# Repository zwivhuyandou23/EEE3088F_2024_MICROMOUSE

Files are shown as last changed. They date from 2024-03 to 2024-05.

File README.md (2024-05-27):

# Welcome to the EEE3088F_2024_MICROMOUSE hardware project

## Name
 2024 Micromouse Project

## Description
The Micromouse Project is a maze-solving robot project designed for the EEE3088F 2024 course. Students will focus on designing and manufacturing sensor and power modules for the micro-mouse, meeting specific project requirements while adhering to a strict budget.

## Features
- Sensor module for detecting obstacles
- Power module for powering the entire system
- Integration with provided motherboard and processor boards

## Project Scenarios
Maze completion.

## Usage
The Micromouse project is intended for educational purposes in the EEE3088F 2024 course. Zwivhuya Ndou and Innocent Makhubela worked on designing, manufacturing, and demonstrating the sensor and power modules for the micro-mouse robot.

## Installation
To access some of the contents on the repo you will need kicad to open the project PCB, Schematics designs and an IDE that supports C programming

## Authors and acknowledgment
Zwivhuya Ndou, Innocent Makhubela

## Contributing

Contributions to the ENVIRO-SENSING-HAT project are welcome! If you have any ideas, bug fixes, or improvements, please follow the guidelines outlined in the [CONTRIBUTING.md](CONTRIBUTING.md) file.

## License

The ENVIRO-SENSING-HAT project is licensed under the MIT License. See the [LICENSE](LICENSE.md) file for more information.

## Project status
Ongoing - part of the EEE3088F 2024 course project, to be carried to the second semester course.

## Contact
If you have any questions or inquiries about the Micromouse project, feel free to contact us at Zwivhuya Ndou(ndxzwi002@myuct.ac.za), Innocent Makhubela ().

Thank you for your interest in the Micromouse project!

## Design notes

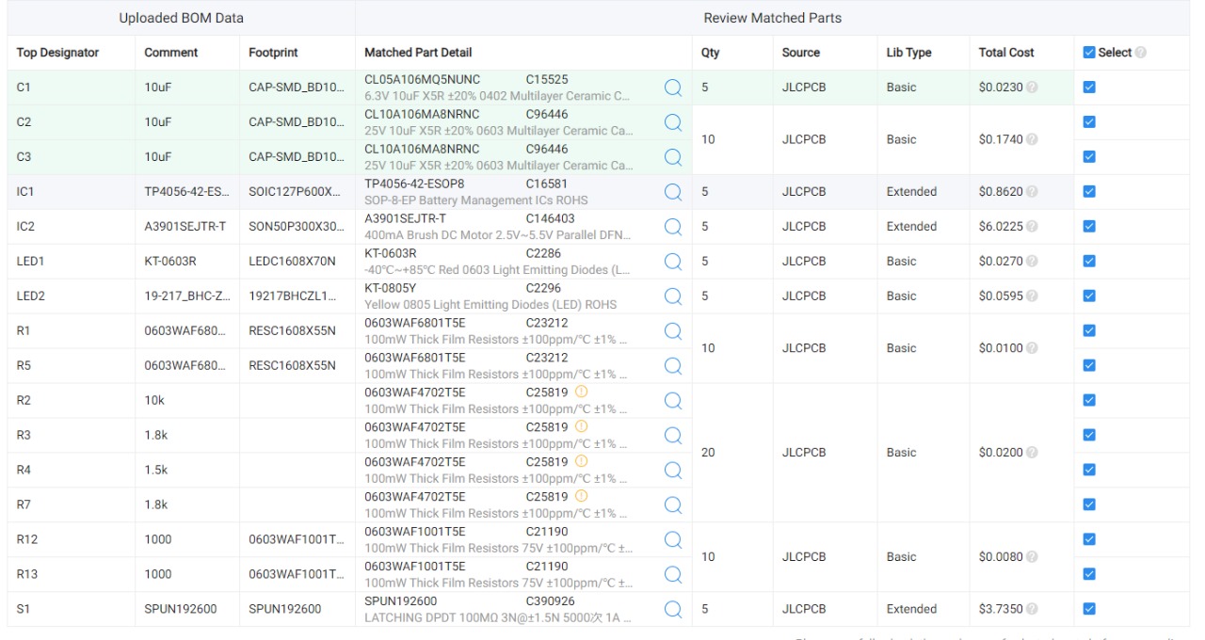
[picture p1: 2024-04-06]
Design/Power/Kicad/production_files/EEE3088F_Project_JLCPCBBOM_MKHINN011.jpg

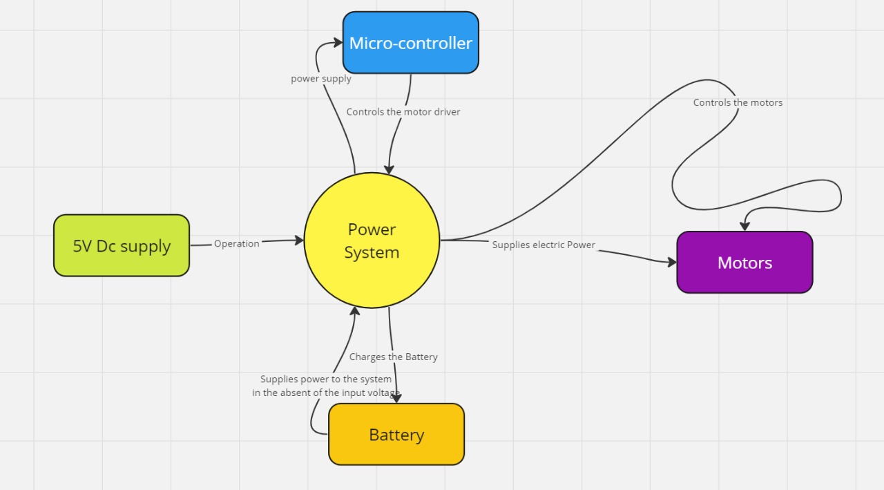
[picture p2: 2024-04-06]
Design/Power/System design/context.jpg

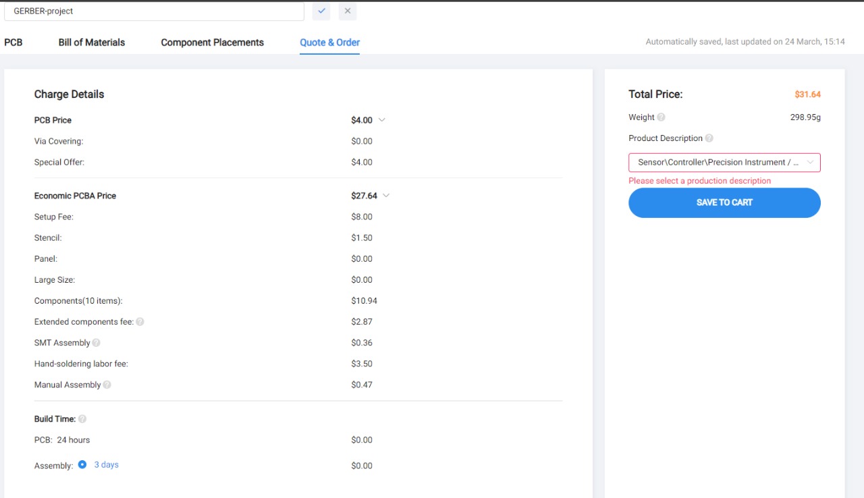
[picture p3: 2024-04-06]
Design/Power/Kicad/production_files/EEE3088F_Project_JLCPCBacceptance_MKHINN011.jpg

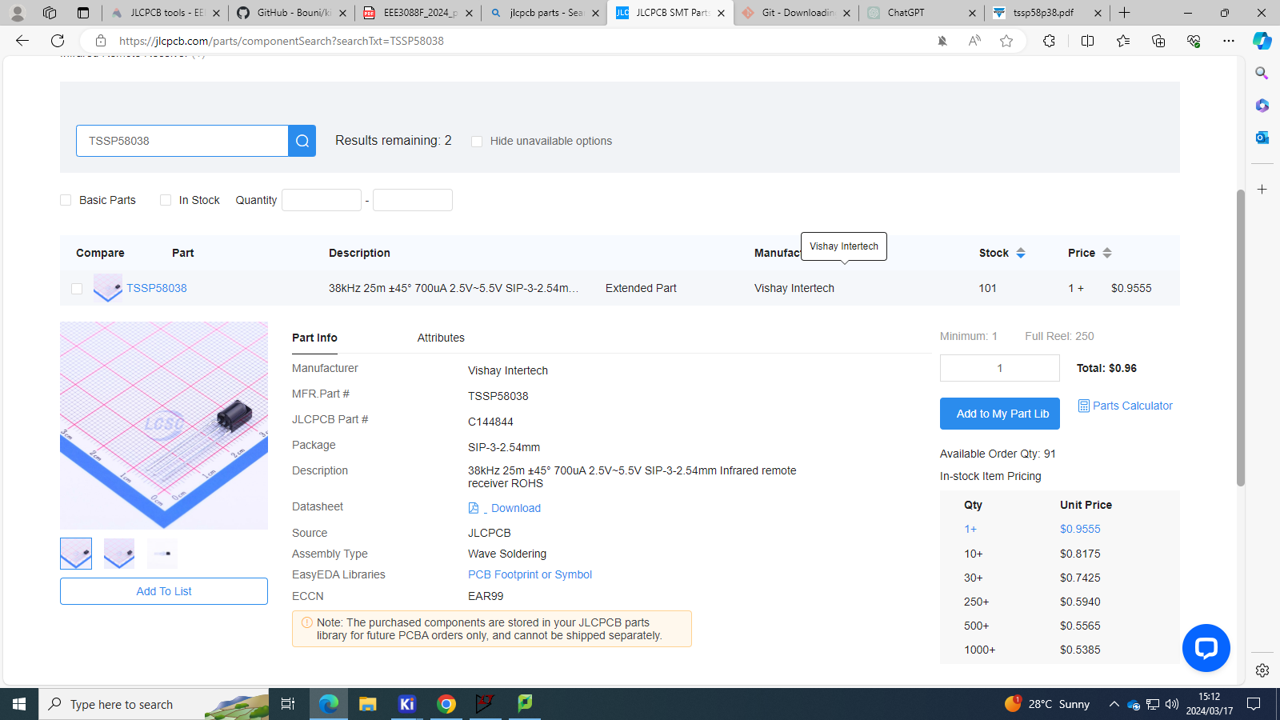
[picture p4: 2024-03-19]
Docs/Screenshot (1).png

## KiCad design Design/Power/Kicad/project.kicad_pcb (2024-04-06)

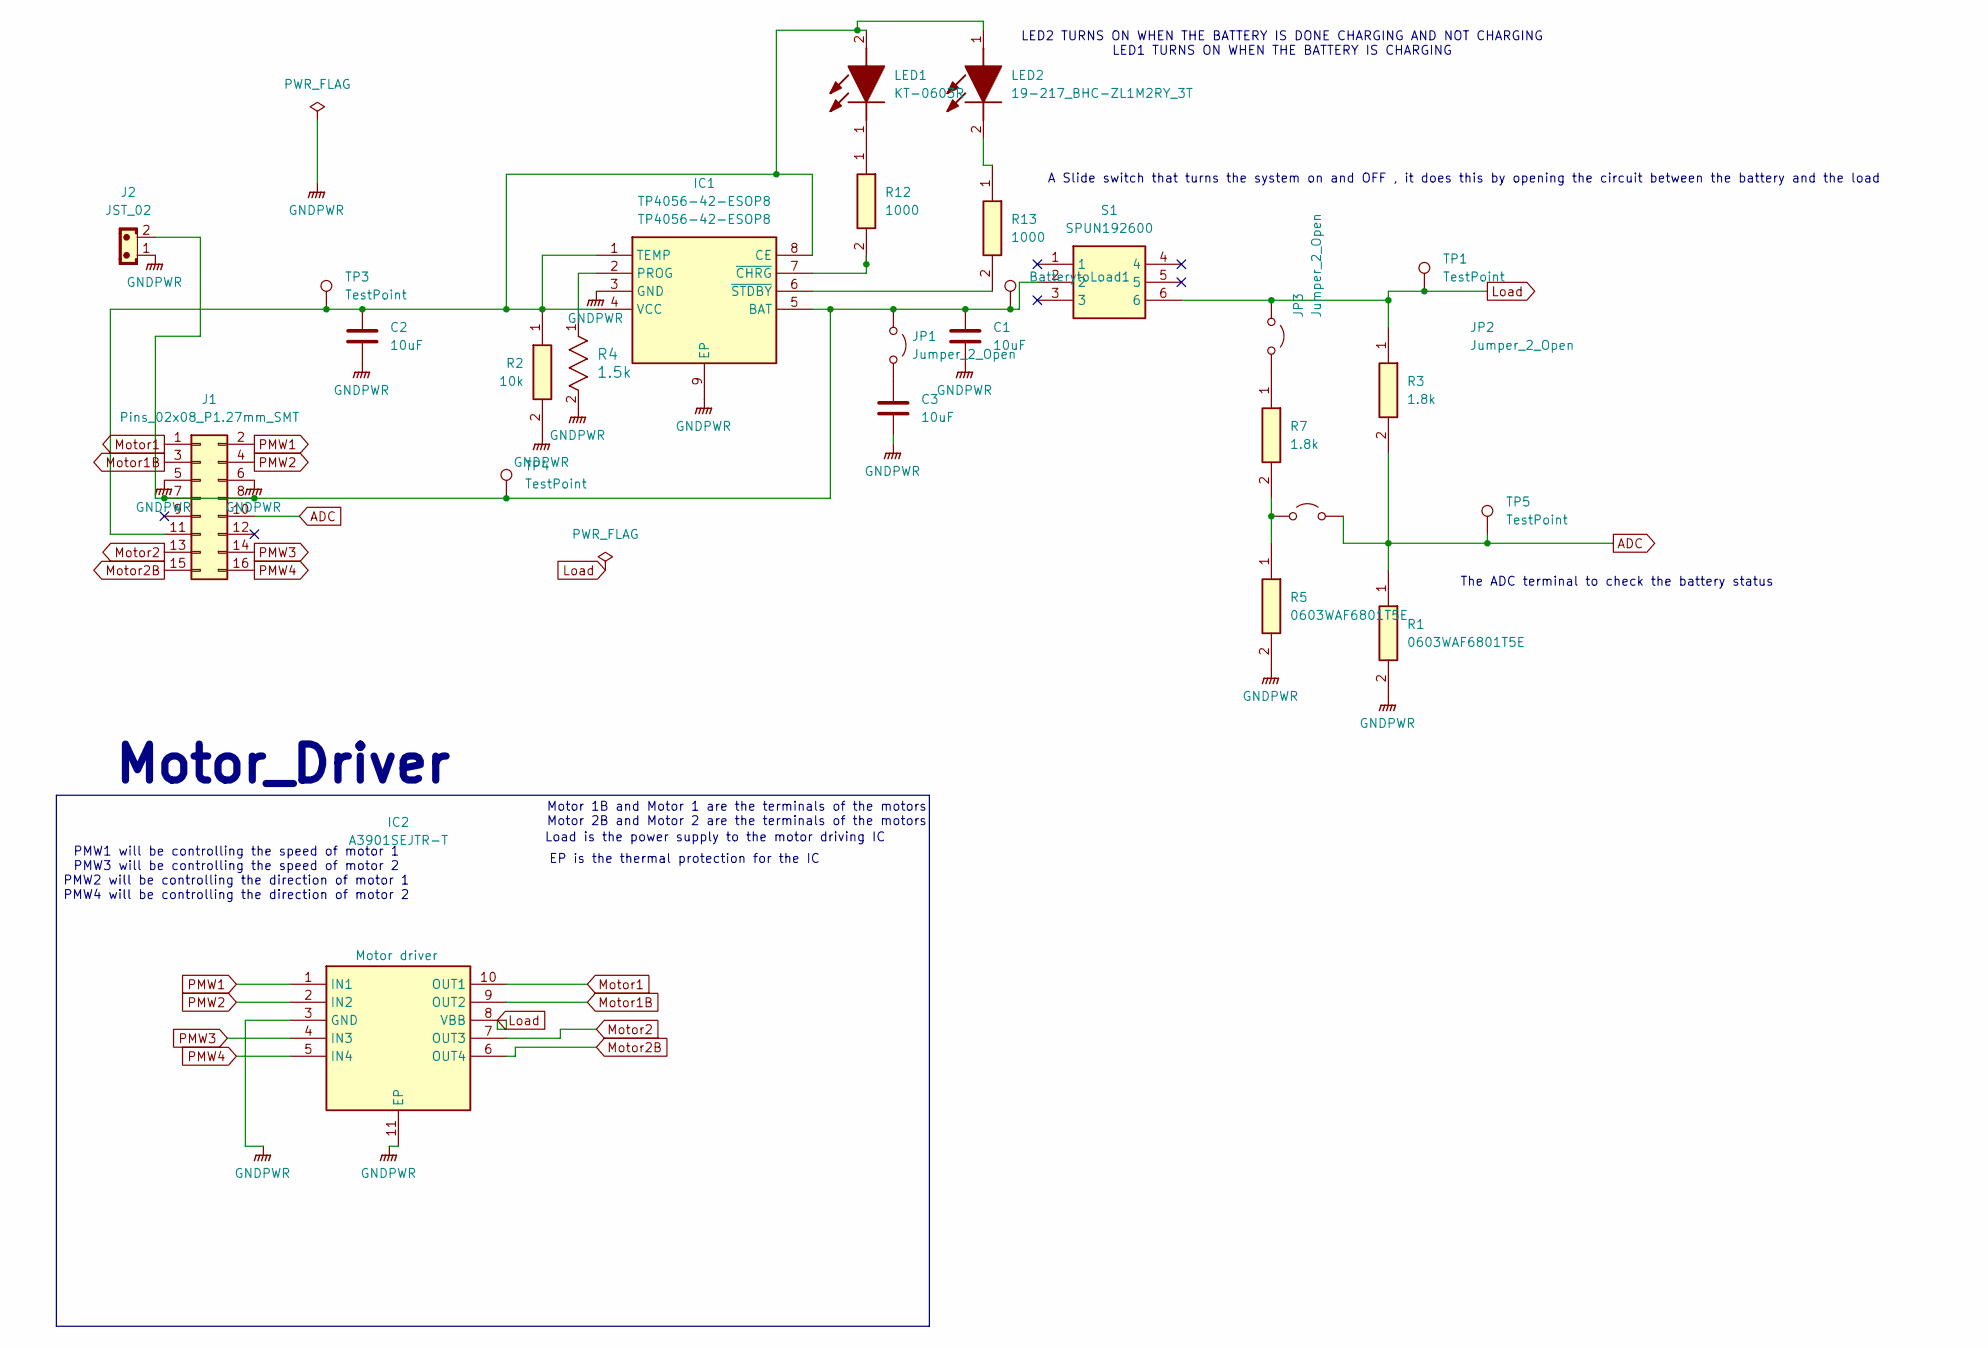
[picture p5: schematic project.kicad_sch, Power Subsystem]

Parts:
BatterytoLoad1: TestPoint; TestPoint_Pad_04
C1, C2, C3: 10uF; CAPC1005X70N
IC1: TP4056-42-ESOP8; SOIC127P600X175-9N; Manufacturer_Part_Number TP4056-42-ESOP8
IC2: A3901SEJTR-T; SON50P300X300X75-11N-D; Manufacturer_Part_Number A3901SEJTR-T; Mouser Part Number Motor driver
J1: Pins_02x08_P1.27mm_SMT; PinHeader_2x08_P2.54mm_Vertical; Part Number FTSH-108-01-F-DV
J2: JST_02; JST_JWPF_B02B-JWPF-SK-R_1x02_P2.00mm_Vertical
JP1, JP2, JP3: Jumper_2_Open; SolderJumper-2_P1.3mm_Open_RoundedPad1.0x1.5mm
LED1: KT-0603R; LEDC1608X70N; Manufacturer_Part_Number KT-0603R
LED2: 19-217_BHC-ZL1M2RY_3T; 19217BHCZL1M2RY3T; Manufacturer_Part_Number 19-217/BHC-ZL1M2RY/3T
R1, R5: 0603WAF6801T5E; RESC1608X55N; Manufacturer_Part_Number 0603WAF6801T5E
R2: 10k; RESC3116X65N; Manufacturer_Part_Number 1206W4F1002T5E
R3, R7: 1.8k; RESC1608X55N; Manufacturer_Part_Number 0603WAF1801T5E
R4: 1.5k; RES_8F1001T5E_UNR
R12: 1000; RESC1608X55N; Manufacturer_Part_Number 0603WAF1001T5E
R13: 1000; SOT95P280X145-5N; Manufacturer_Part_Number 0603WAF1001T5E
S1: SPUN192600; Manufacturer_Part_Number SPUN192600; Mouser Part Number 688-SPUN192600
TP1, TP3, TP4, TP5: TestPoint; TestPoint_Pad_04

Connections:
ADC: J1.10 (GND), JP3.2 (B), R1.1, R3.2, TP5.1; also elsewhere on the board
GNDPWR: C1.2, C2.2, C3.2, IC1.3 (GND), IC1.9 (EP), IC2.3 (GND), IC2.11 (EP), J1.5 (+12V), J1.6, J2.1, R1.2, R2.2, R4.2, R5.2
Load: IC2.8 (VBB), JP2.1 (A), R3.1, S1.6, TP1.1
Motor1: IC2.10 (OUT1), J1.1
Motor1B: IC2.9 (OUT2), J1.3
Motor2: IC2.7 (OUT3), J1.13 (-12)
Motor2B: IC2.6 (OUT4), J1.15 (-12V)
unnamed: BatterytoLoad1.1, C1.1, IC1.5 (BAT), J1.7 (12V), J1.8 (+12V), J2.2, JP1.1 (A), S1.2, TP4.1
unnamed 8: C2.1, IC1.1 (TEMP), IC1.4 (VCC), IC1.8 (CE), J1.11 (GND), LED1.2 (A), LED2.1 (A), R2.1, TP3.1; also elsewhere on the board
unnamed: IC1.2 (PROG), R4.1
unnamed: IC1.7 (~CHRG), R12.2
unnamed: IC1.6 (~STDBY), R13.2
unnamed: C3.1, JP1.2 (B)
unnamed: JP2.2 (B), R7.1
unnamed: JP3.1 (A), R5.1, R7.2
unnamed: LED1.1 (K), R12.1
unnamed: LED2.2 (K), R13.1
PMW1: IC2.1 (IN1), J1.2
PMW2: IC2.2 (IN2), J1.4
PMW3: IC2.4 (IN3), J1.14 (-12V)
PMW4: IC2.5 (IN4), J1.16

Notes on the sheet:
Motor 1B and Motor 1 are the terminals of the motors
PMW1 will be controlling the speed of motor 1 PMW3 will be controlling the speed of motor 2 PMW2 will be controlling the direction of motor 1 PMW4 will be controlling the direction of motor 2
The ADC terminal to check the battery status
Motor_Driver
Motor 2B and Motor 2 are the terminals of the motors
Load is the power supply to the motor driving IC
LED2 TURNS ON WHEN THE BATTERY IS DONE CHARGING AND NOT CHARGING LED1 TURNS ON WHEN THE BATTERY IS CHARGING
A Slide switch that turns the system on and OFF , it does this by opening the circuit between the battery and the load
EP is the thermal protection for the IC

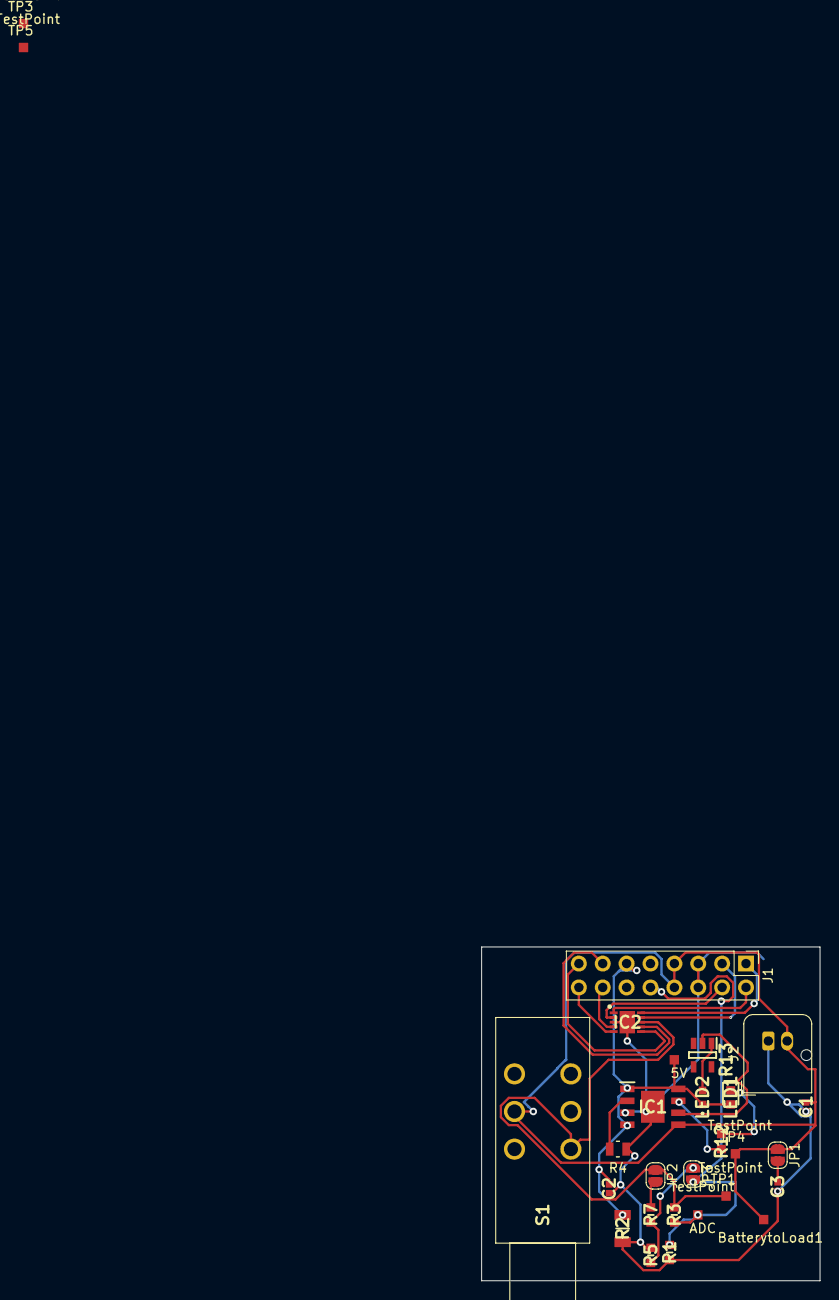
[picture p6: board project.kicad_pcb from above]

Board: 2 copper layers, 36.0 x 35.5 mm, 28 parts (0 on the bottom side), 21 nets.

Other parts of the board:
5V: TestPoint; TestPoint_Pad_04
ADC: TestPoint; TestPoint_Pad_04

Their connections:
ADC: ADC.1; also elsewhere on the board
unnamed 8: 5V.1; also elsewhere on the board

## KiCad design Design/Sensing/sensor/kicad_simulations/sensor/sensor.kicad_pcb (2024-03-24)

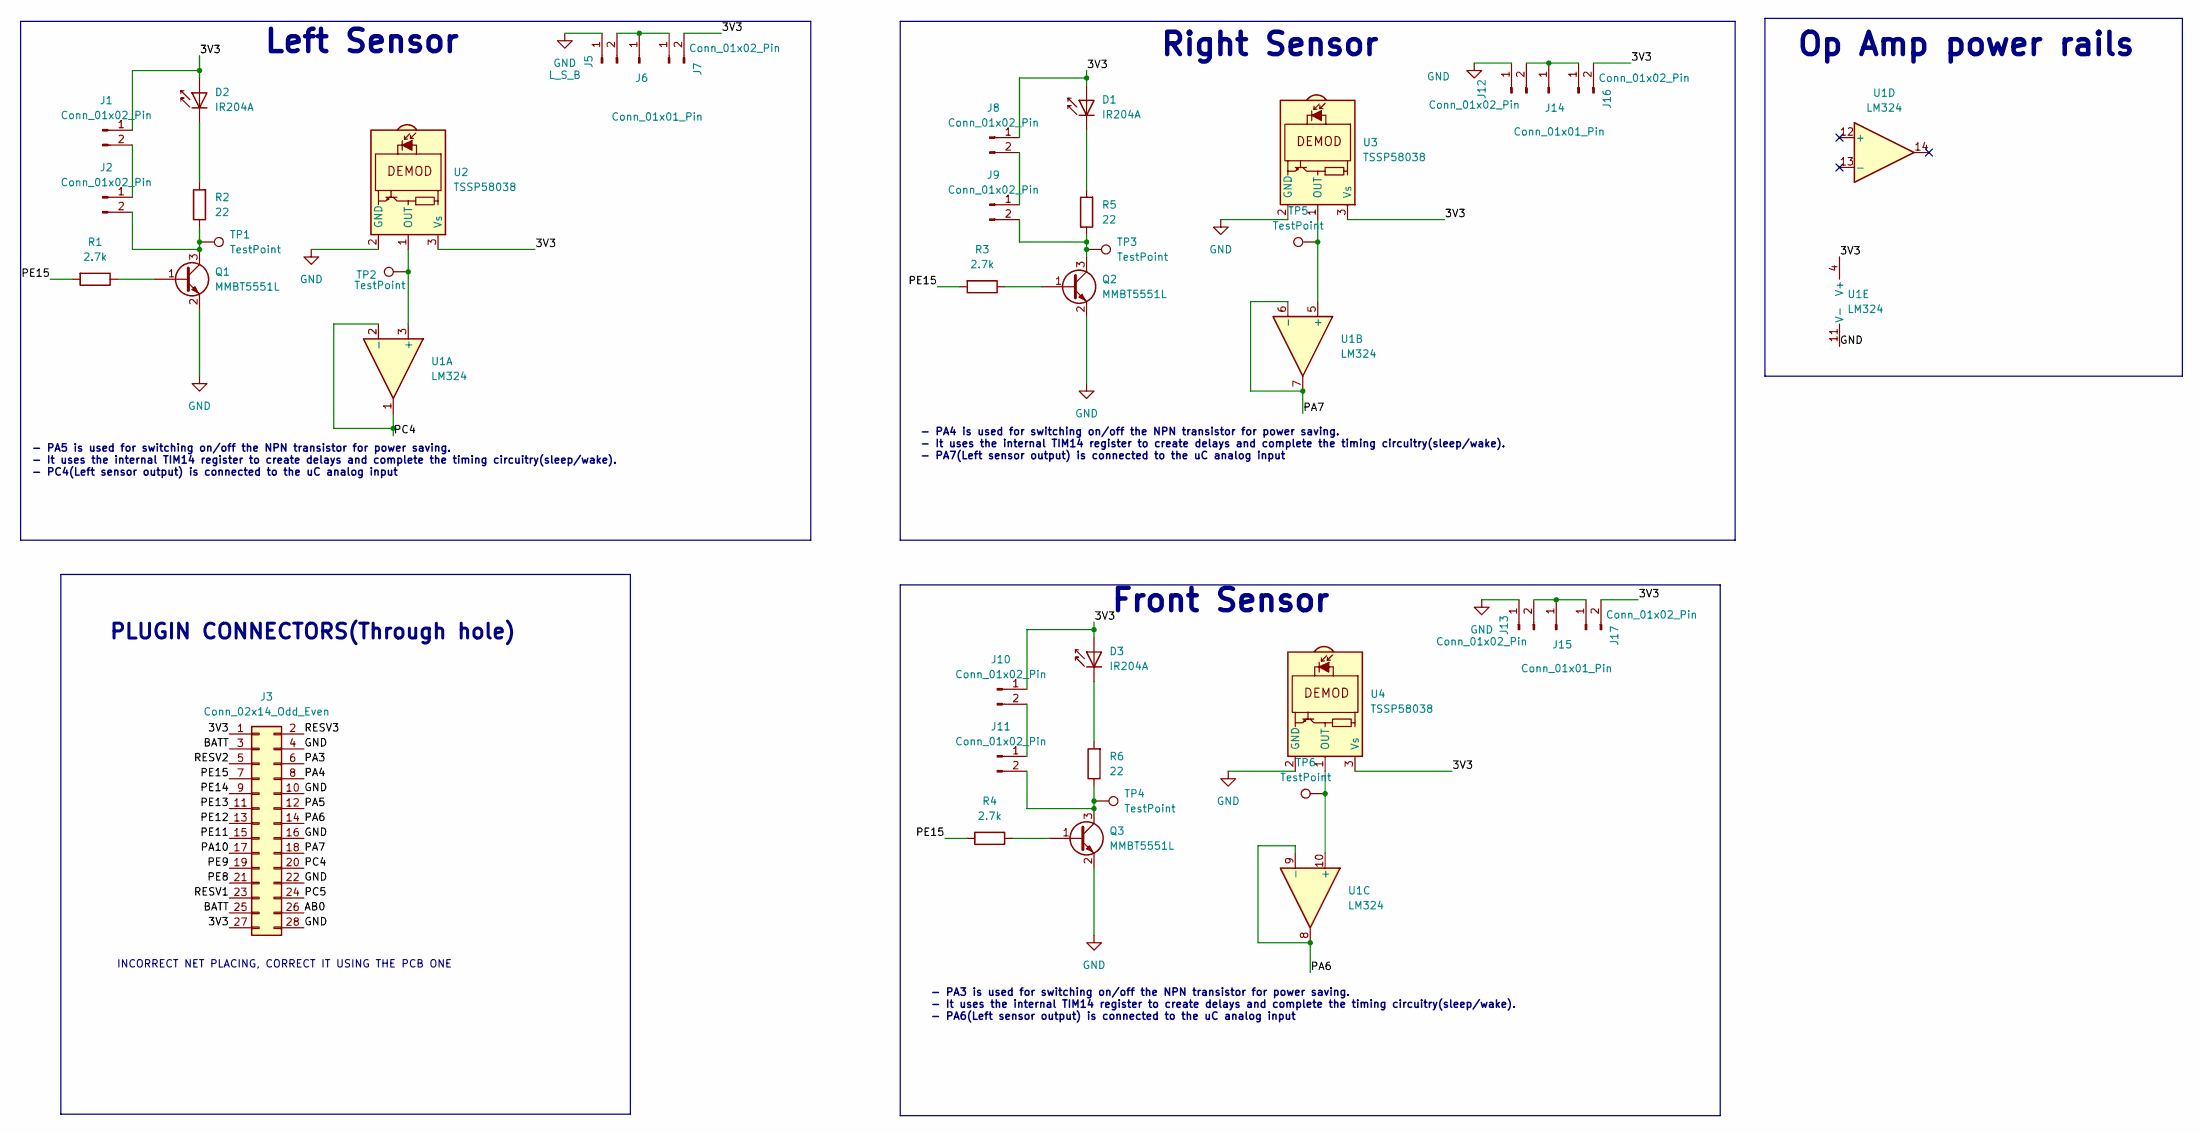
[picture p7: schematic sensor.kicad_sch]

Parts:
D1, D2, D3: IR204A; LED_D3.0mm_Horizontal_O1.27mm_Z2.0mm_IRBlack
J1, J2, J7, J8, J9, J10, J11, J12, J13, J16, J17: Conn_01x02_Pin; PinHeader_1x02_P2.54mm_Vertical
J3: Conn_02x14_Odd_Even; PinHeader_2x14_P2.54mm_Vertical
J5: L_S_B; PinHeader_1x02_P2.54mm_Vertical
J6, J14, J15: Conn_01x01_Pin; PinHeader_1x01_P2.54mm_Vertical
Q1, Q2, Q3: MMBT5551L; SOT-23
R1, R3, R4: 2.7k; R_0805_2012Metric
R2, R5, R6: 22; R_0805_2012Metric
TP1, TP2, TP3, TP4, TP5, TP6: TestPoint; TestPoint_Pad_D1.0mm
U1: LM324; SOIC-14_3.9x8.7mm_P1.27mm
U2, U3, U4: TSSP58038; Vishay_MINICAST-3Pin

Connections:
/3V3: D1.2 (A), D2.2 (A), D3.2 (A), J1.1, J3.1, J3.27, J7.2, J8.1, J10.1, J16.2, J17.2, U1.4 (V+), U2.3 (Vs), U3.3 (Vs), U4.3 (Vs)
/AB0: J3.26
/BATT: J3.3, J3.25
/PA3: J3.6
/PA4: J3.8
/PA5: J3.12
/PA6: J3.14, U1.8, U1.9 (-)
/PA7: J3.18, U1.6 (-), U1.7
/PA10: J3.17
/PC4: J3.20, U1.1, U1.2 (-)
/PC5: J3.24
/PE8: J3.21
/PE9: J3.19
/PE11: J3.15
/PE12: J3.13
/PE13: J3.11
/PE14: J3.9
/PE15: J3.7, R1.2, R3.2, R4.2
/RESV1: J3.23
/RESV2: J3.5
/RESV3: J3.2
GND: J3.4, J3.10, J3.16, J3.22, J3.28, J5.1, J12.1, J13.1, Q1.2 (E), Q2.2 (E), Q3.2 (E), U1.11 (V-), U2.2 (GND), U3.2 (GND), U4.2 (GND)
unnamed: D1.1 (K), R5.2
unnamed: D2.1 (K), R2.2
unnamed: D3.1 (K), R6.2
unnamed: J1.2, J2.1
unnamed: J2.2, Q1.3 (C), R2.1, TP1.1
unnamed: J5.2, J6.1, J7.1
unnamed: J8.2, J9.1
unnamed: J9.2, Q2.3 (C), R5.1, TP3.1
unnamed: J10.2, J11.1
unnamed: J11.2, Q3.3 (C), R6.1, TP4.1
unnamed: J12.2, J14.1, J16.1
unnamed: J13.2, J15.1, J17.1
unnamed: Q1.1 (B), R1.1
unnamed: Q2.1 (B), R3.1
unnamed: Q3.1 (B), R4.1
unnamed: TP2.1, U1.3 (+), U2.1 (OUT)
unnamed: TP5.1, U1.5 (+), U3.1 (OUT)
unnamed: TP6.1, U1.10 (+), U4.1 (OUT)

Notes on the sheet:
- PA5 is used for switching on/off the NPN transistor for power saving. - It uses the internal TIM14 register to create delays and complete the timing circuitry(sleep/wake). - PC4(Left sensor output) is connected to the uC analog input
- PA4 is used for switching on/off the NPN transistor for power saving. - It uses the internal TIM14 register to create delays and complete the timing circuitry(sleep/wake). - PA7(Left sensor output) is connected to the uC analog input
Op Amp power rails
- PA3 is used for switching on/off the NPN transistor for power saving. - It uses the internal TIM14 register to create delays and complete the timing circuitry(sleep/wake). - PA6(Left sensor output) is connected to the uC analog input
Left Sensor
PLUGIN CONNECTORS(Through hole)
Front Sensor
INCORRECT NET PLACING, CORRECT IT USING THE PCB ONE
Right Sensor

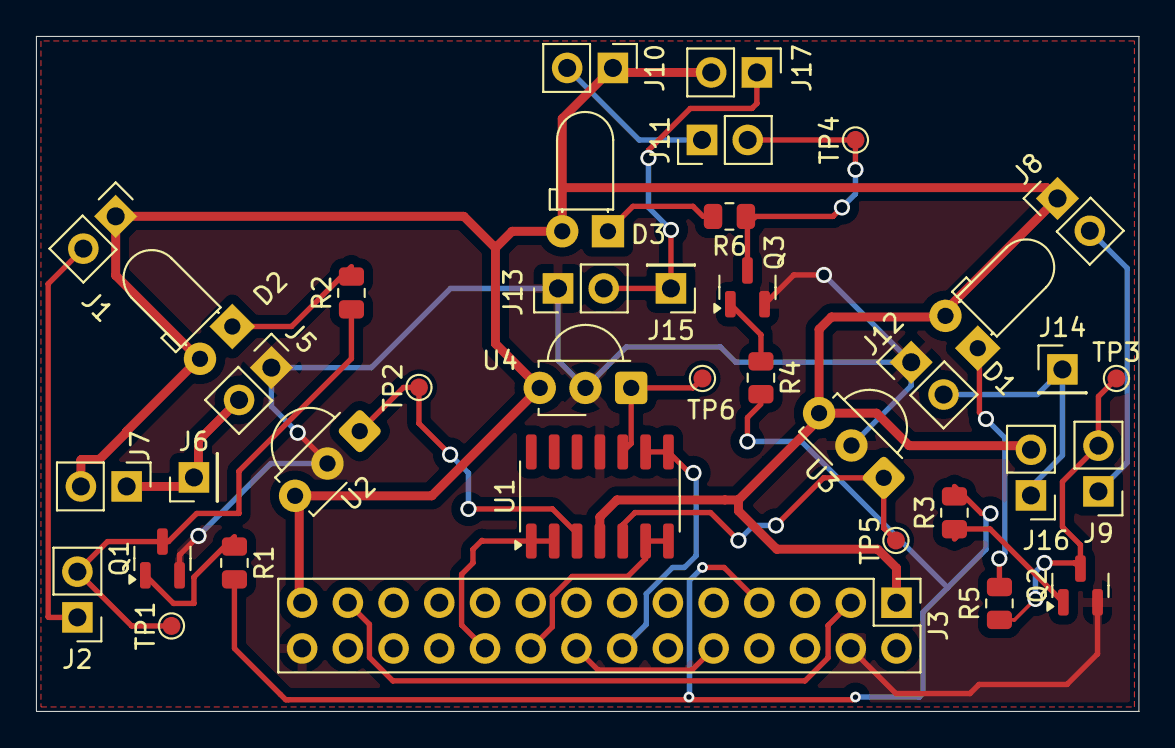
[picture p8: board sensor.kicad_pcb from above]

Board: 2 copper layers, 61.2 x 37.5 mm, 38 parts (0 on the bottom side), 25 nets.

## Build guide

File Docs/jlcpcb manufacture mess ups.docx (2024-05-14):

Expected mess ups.

The jlcpcb view reverse polarised my IR leds

Will have to desolder

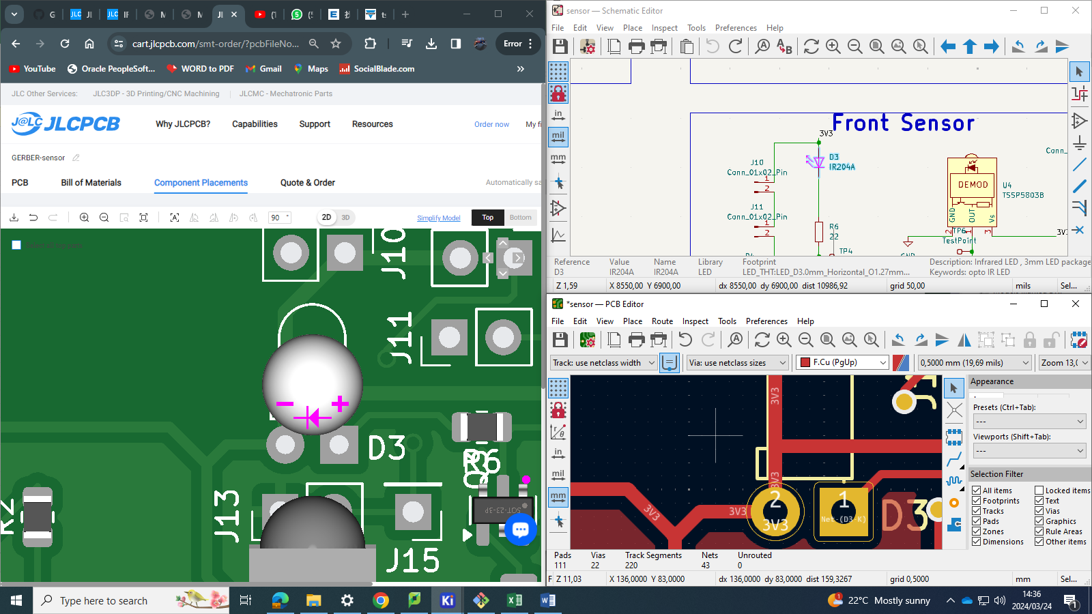
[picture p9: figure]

Final pcb

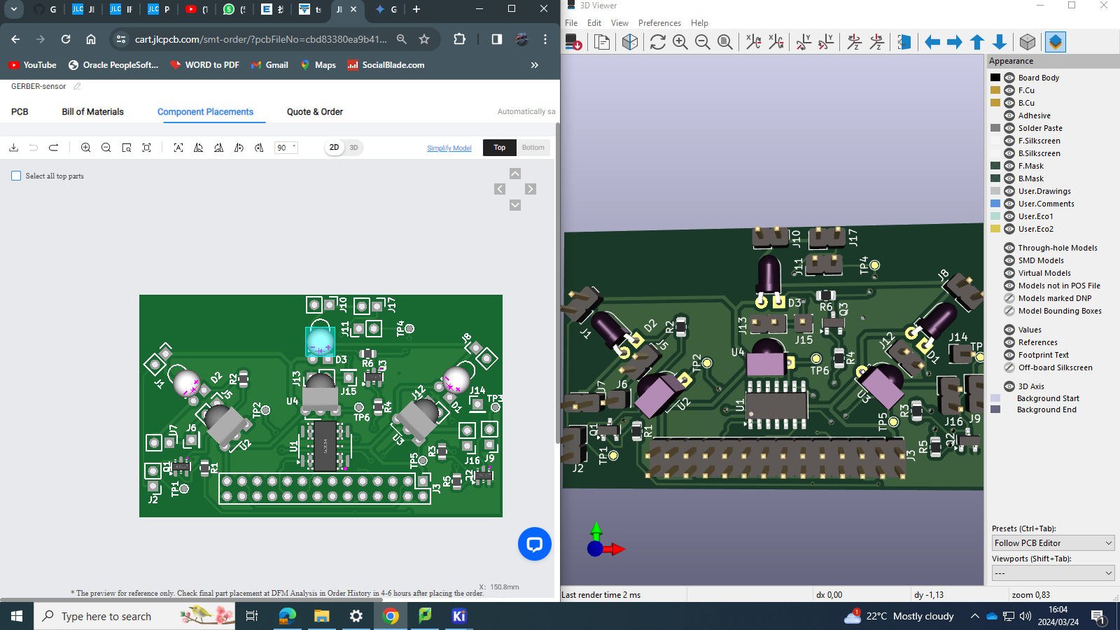
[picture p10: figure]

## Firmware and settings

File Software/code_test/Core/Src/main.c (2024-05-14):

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
/* Includes ------------------------------------------------------------------*/
#include "main.h"

/* USER CODE BEGIN Includes */
#include "string.h"
#include "stm32f0xx_hal.h"
#include <stdio.h>
#include "lcd_stm32f0.h"
/* USER CODE END Includes */

ADC_HandleTypeDef hadc;

/* USER CODE BEGIN PV */


#define THRESHOLD_LOW  431 // ADC threshold for LED off
#define THRESHOLD_HIGH 539 // ADC threshold for LED on

#define EMITTER1_PIN GPIO_PIN_1
#define EMITTER1_PORT GPIOB
#define EMITTER2_PIN GPIO_PIN_2
#define EMITTER2_PORT GPIOB
#define EMITTER3_PIN GPIO_PIN_10
#define EMITTER3_PORT GPIOB

uint16_t adc_value_front_sensor;
uint16_t adc_value_right_sensor;
uint16_t adc_value_left_sensor;
uint16_t adc_value;
uint8_t channel = 1;


char str_adc_value_front[100];
char str_adc_value_right[100];
char str_adc_value_left[100];



/* USER CODE END PV */

void SystemClock_Config(void);
static void MX_GPIO_Init(void);
static void MX_ADC_Init(void);
/* USER CODE BEGIN PFP */
uint16_t read_adc();
void adc_set_channel(uint8_t num);

/* USER CODE END PFP */

void delay_ms(uint32_t ms) {
    HAL_Delay(ms);
}
/**
  * @brief  The application entry point.
  * @retval int
  */
int main(void)
{
  /* MCU Configuration--------------------------------------------------------*/

  /* Reset of all peripherals, Initializes the Flash interface and the Systick. */
  HAL_Init();

  /* Configure the system clock */
  SystemClock_Config();

  /* Initialize all configured peripherals */
  MX_GPIO_Init();
  MX_ADC_Init();
  /* USER CODE BEGIN 2 */
  lcd_init(); // set up LCD lines and send initialisation commands
  lcd_command(LCD_CLEAR_DISPLAY);

  //lcd_command(LCD_GOTO_LINE_2);


  /* USER CODE END 2 */

  /* Infinite loop */
  /* USER CODE BEGIN WHILE */
  while (1)
  {
    /* USER CODE END WHILE */

	  /* USER CODE END WHILE */

    /* USER CODE BEGIN 3 */

	     ADC1->CHSELR = ADC_CHSELR_CHSEL1;
		      HAL_Delay(1);
			 // adc_set_channel(channel);
			  adc_value_front_sensor = read_adc() ;
			 HAL_ADC_Stop(&hadc);

				 if(adc_value_front_sensor > 539) {
					 HAL_GPIO_WritePin(GPIOB, GPIO_PIN_6, GPIO_PIN_SET);
				  }
				 else if (adc_value_front_sensor <= 431){
				 HAL_GPIO_WritePin(GPIOB, GPIO_PIN_6, GPIO_PIN_RESET);

			  }


			  ADC1->CHSELR = ADC_CHSELR_CHSEL2;
			  HAL_Delay(1);
			 // adc_set_channel(channel);
			  adc_value_right_sensor = read_adc() ;
			  HAL_ADC_Stop(&hadc);

			 if(adc_value_right_sensor > 539) {
			 		HAL_GPIO_WritePin(GPIOB, GPIO_PIN_5, GPIO_PIN_SET);
			 		  }
			 else if (adc_value_right_sensor <= 431){
			 		 HAL_GPIO_WritePin(GPIOB, GPIO_PIN_5, GPIO_PIN_RESET);
			 		  }

			 ADC1->CHSELR = ADC_CHSELR_CHSEL3;
			 HAL_Delay(1);
			// adc_set_channel(channel);
			 adc_value_left_sensor = read_adc() ;
			 HAL_ADC_Stop(&hadc);

			 if(adc_value_left_sensor > 539) {
			 	HAL_GPIO_WritePin(GPIOB, GPIO_PIN_7, GPIO_PIN_SET);
			 		  }
			 else if (adc_value_left_sensor <= 431){
			 	 HAL_GPIO_WritePin(GPIOB, GPIO_PIN_7, GPIO_PIN_RESET);
			 		  }

			//  HAL_Delay(500);



			  HAL_Delay(100);


		        // Switch on emitters in sequence
			HAL_GPIO_WritePin(EMITTER1_PORT, EMITTER1_PIN, GPIO_PIN_SET);
			delay_ms(100);
			HAL_GPIO_WritePin(EMITTER1_PORT, EMITTER1_PIN, GPIO_PIN_RESET);

			HAL_GPIO_WritePin(EMITTER2_PORT, EMITTER2_PIN, GPIO_PIN_SET);
			delay_ms(100);
			HAL_GPIO_WritePin(EMITTER2_PORT, EMITTER2_PIN, GPIO_PIN_RESET);

			HAL_GPIO_WritePin(EMITTER3_PORT, EMITTER3_PIN, GPIO_PIN_SET);
			delay_ms(100);
			HAL_GPIO_WritePin(EMITTER3_PORT, EMITTER3_PIN, GPIO_PIN_RESET);

			  /*
		  channel++;
		  sprintf(str_adc_value_front, "F_S_ADC = %d", adc_value_front_sensor);
		  sprintf(str_adc_value_right, "R_S_ADC = %d", adc_value_right_sensor);
		  sprintf(str_adc_value_left, "L_S_ADC = %d", adc_value_left_sensor);

		  lcd_command(LCD_GOTO_LINE_2);

		  lcd_two_line_write(str_adc_value_front, str_adc_value_right );
		  HAL_Delay(1000);
		  lcd_command(LCD_CLEAR_DISPLAY);
		  lcd_command(LCD_GOTO_LINE_2);
		  lcd_string(str_adc_value_left);
		 HAL_Delay(1000);

		  lcd_command(LCD_CLEAR_DISPLAY);
		  HAL_Delay(100);
		  HAL_GPIO_WritePin(GPIOB, GPIO_PIN_0, GPIO_PIN_RESET);//PWM Sleep moode
		  HAL_Delay(100);*/
  }
  /* USER CODE END 3 */
}

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
/* USER CODE BEGIN 4 */
uint16_t read_adc()
{

	    HAL_ADC_Start(&hadc);
	    while(HAL_ADC_PollForConversion(&hadc,5)!= HAL_OK);
	    adc_value = HAL_ADC_GetValue(&hadc);
	    return adc_value;

}
void adc_set_channel(uint8_t num) {
    ADC_ChannelConfTypeDef sConfig = {0};

    if (num==1) {
      sConfig.Channel = ADC_CHANNEL_1;
    } else if (num==2){
      sConfig.Channel = ADC_CHANNEL_2;
    }
    else
    {
    	sConfig.Channel = ADC_CHANNEL_3;
    	channel = 0;
    }
    sConfig.Rank = ADC_RANK_CHANNEL_NUMBER;
    sConfig.SamplingTime = ADC_SAMPLETIME_1CYCLE_5;
    if (HAL_ADC_ConfigChannel(&hadc, &sConfig) != HAL_OK)
    {
      Error_Handler();
    }
}
/* USER CODE END 4 */
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


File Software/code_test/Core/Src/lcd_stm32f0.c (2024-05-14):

/*
Copyright (C) Samuel Ginsberg 2004
Porting to STM32F0 dev board by James Gowans, 2014
LCD lines are as follows:
LCD_RS = PC14
LCD_E = PC15
LCD_D4 = PB8
LCD_D5 = PB9
LCD_D6 = PA12
LCD_D7 = PA15
*/

#include "lcd_stm32f0.h"

enum TypeOfCharacter {
  COMMAND = 0,
  TEXT = 1
};


static void delay (uint32_t microseconds);
static void pulse_strobe (void);
static void lcd_put (uint8_t character, enum TypeOfCharacter ch_type);
static void lcd_write4bits(uint8_t value);

//============================================================================

void lcd_string(uint8_t *string_to_print) {
  uint32_t count=0;
  while (string_to_print[count] != 0) {
    lcd_put (string_to_print[count], TEXT);
    delay(43); // a DRAM write requires at least 43 us execution time
    count++;
  }
}
void lcd_two_line_write(uint8_t* line1, uint8_t* line2) {
  lcd_command(LCD_CLEAR_DISPLAY);
  lcd_string(line1);
  lcd_command(LCD_GOTO_LINE_2);
  lcd_string(line2);
}

//============================================================================

void lcd_init () {
  /*This function sets up the port lines for the LCD and initializes
  the LCD module for use.*/
  // set the relevant pins to outputs
  RCC->AHBENR |= RCC_AHBENR_GPIOCEN;
  RCC->AHBENR |= RCC_AHBENR_GPIOBEN; 
  RCC->AHBENR |= RCC_AHBENR_GPIOAEN; 
  GPIOC->MODER |= GPIO_MODER_MODER14_0;
  GPIOC->MODER |= GPIO_MODER_MODER15_0;
  GPIOB->MODER |= GPIO_MODER_MODER8_0;
  GPIOB->MODER |= GPIO_MODER_MODER9_0;
  GPIOA->MODER |= GPIO_MODER_MODER12_0;
  GPIOA->MODER |= GPIO_MODER_MODER15_0;

  delay(30000); //allow the LCD 30 ms power up time
  // in case in 2nd nibble of 4 bit tansfer, this goes to 1st nibble
  // if byte in 8-bit mode, keeps in 8-bit mode
  lcd_write4bits(0x03);   
  delay(4100);
  lcd_write4bits(0x03);  // garanteed to be byte of 8-bit data for first byte of 4-bit.
  delay(39);
  lcd_write4bits(0x03); // necessary in case this is the 2nd nibble of 4-bit transfer.
  delay(39);
  // switch to 4-bit. This will latch in a byte as it's garanteed to now be in 8-bit
  lcd_write4bits(0x02);   
  delay(39);
  lcd_command(LCD_FOUR_BIT_TWO_LINE_MODE); //0x28
  lcd_command(LCD_DISPLAY_OFF); // 0x08
  lcd_command(LCD_CLEAR_DISPLAY); // 0x01
  lcd_command(LCD_DISPLAY_ON); // 0x0C
}

//============================================================================

void lcd_command (enum LcdCommand command) {
  //This function sends a command to the LCD. 
  //Care is taken not to interfere with the other lines on the port.
  lcd_put((uint8_t)command, COMMAND);
  delay(1530); // 1.53 ms is the maximum delay we should need for any command.
  // TODO: fix the above to have variable lengths as required by different commands.
}

//============================================================================

static void lcd_put (uint8_t character, enum TypeOfCharacter ch_type) {
    //Puts a single character on the LCD at the next position on the screen.
    //The character to be printed is in the input parameter. For numbers, letters 
    //and other common characters the ASCII code will produce correct display.
    //Refer to the Hitachi HD44780 datasheet for full character set information.
    if (ch_type == TEXT) {
        GPIOC->BSRR |= GPIO_BSRR_BS_14;// pull RS (PC14) high
    } else if (ch_type == COMMAND) {
        GPIOC->BSRR |= GPIO_BSRR_BR_14;// pull RS (PC14) low
    }
    // write upper nibble
    lcd_write4bits(character >> 4);
    // write lower nibble
    lcd_write4bits(character);
}

// This function outputs the lower 4 bits onto the data lines
static void lcd_write4bits(uint8_t character) {
  // lower nibble to data lines
  if ((character & 0x08) != 0) {
    GPIOA->BSRR |= GPIO_BSRR_BS_15;
  } else {
    GPIOA->BSRR |= GPIO_BSRR_BR_15;
  }
  if ((character & 0x04) != 0) {
    GPIOA->BSRR |= GPIO_BSRR_BS_12;
  } else {
    GPIOA->BSRR |= GPIO_BSRR_BR_12;
  }
  if ((character & 0x02) != 0) {
    GPIOB->BSRR |= GPIO_BSRR_BS_9;
  } else {
    GPIOB->BSRR |= GPIO_BSRR_BR_9;
  } 
  if ((character & 0x01) != 0) {
    GPIOB->BSRR |= GPIO_BSRR_BS_8;
  } else {
    GPIOB->BSRR |= GPIO_BSRR_BR_8;
  }
  pulse_strobe ();
}

//============================================================================


static void delay(uint32_t microseconds) {
  /* Hangs for specified number of microseconds. */
  volatile uint32_t counter = 0;
  microseconds *= 3;
  for(; counter<microseconds; counter++) {
    __asm("nop");
    __asm("nop");
  }
}

static void pulse_strobe (void) {
  //Pulse the strobe line of the LCD to indicate that data is ready.
  delay(1);
  GPIOC->BSRR |= GPIO_BSRR_BS_15;// pull E (PC15) high
  delay(1);
  GPIOC->BSRR |= GPIO_BSRR_BR_15;// pull E (PC15) low
  delay(1);
}                     

//============================================================================

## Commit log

2024-03-19 Folders for Power and Sensing created for each subsytem's files
    [Front Sensor.kicad_sch, Left Sensor.kicad_sch, Right Sensor.kicad_sch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]
2024-03-19 Repo created and necessary folders created
    [Front Sensor.kicad_sch, Left Sensor.kicad_sch, Right Sensor.kicad_sch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]
2024-03-19 Added new schematic
    [Right Sensor.kicad_sch]
2024-03-19 Resistor values for emitter circuit done, still have to name the circuits properly
    [Front Sensor.kicad_sch, Left Sensor.kicad_sch, Right Sensor.kicad_sch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]
2024-03-21 Sensing schematics done, the next stage is working on pcb component placement
    [Front Sensor.kicad_sch, Left Sensor.kicad_sch, Right Sensor.kicad_sch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]
2024-03-21 Footprints assigned
    [sensor.kicad_sch]
2024-03-21 All Footprints assigned
    [sensor.kicad_pcb]
2024-03-21 PCB components placed but unrooted
    [sensor.kicad_pcb, sensor.kicad_sch]
2024-03-22 working on pcb
    [sensor.kicad_pcb]
2024-03-22 PCB placement done, now need to root/make track connections
    [sensor.kicad_pcb, sensor.kicad_sch]
2024-03-22 PCB track done but still have 23 unrouted
    [sensor.kicad_pcb, sensor.kicad_sch]
2024-03-22 Only two unrouted and 3 errors remaining
    [sensor.kicad_pcb, sensor.kicad_sch]
2024-03-22 pcb placement redo
    [sensor.kicad_pcb, sensor.kicad_sch]
2024-03-24 Routed correct design
    [BOM-sensor.csv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]
2024-03-24 Gerber files generated
    [BOM-sensor.csv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]
2024-03-24 IR change
    [sensor.kicad_pcb, sensor.kicad_sch]
2024-03-24 new sensor
2024-03-24 Trace length sorted
    [sensor.kicad_pcb]
2024-03-24 gerber files generated, pcb quote 8 in total and under the budget
    [sensor.kicad_pcb]
2024-03-24 Gerber files done
    [BOM-sensor.csv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]
2024-03-24 ensured that net names in the connectors matches the label in th project
    [sensor.kicad_pcb, sensor.kicad_sch]
2024-03-24 Final gerber files generated
    [sensor.kicad_pcb]
2024-03-24 Gerbers due for submission
    [BOM-sensor.csv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]
2024-04-02 Create Power
2024-04-02 Rename Design/Power to Design/Power /EEE3088F_2024_project_description_v5.pdf
2024-04-02 Create Schematic
2024-04-02 The schematic of the subsystem without description
    [project.kicad_sch]
2024-04-02 Rename Design/Power/System design to Design/Power/System design /dumbfile.pdf
    ignore the file (used to create a folder
2024-04-06 Add files via upload
    All the KICAD FILES FOR THE PROJECT
    [BOM-project.csv, project.kicad_pcb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]
2024-04-06 Delete Design/Power/System design directory
    the directory is a duplicste
    [BOM-project.csv, project.kicad_pcb, project.kicad_sch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]
2024-04-06 Delete Design/Power/System design directory
    duplicate file
2024-04-16 Docs folder created
    [Front Sensor.kicad_sch, Left Sensor.kicad_sch, Right Sensor.kicad_sch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]
2024-04-16 Trying to make the repo clean
    [Front Sensor.kicad_sch, Left Sensor.kicad_sch, Right Sensor.kicad_sch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]
2024-04-19 Updated the schematic
    [sensor.kicad_sch]
2024-04-19 Updated the schematicgit
    [BOM-sensor.csv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]
2024-04-26 Libraries for demo updated
    [sensor.kicad_sch]
2024-05-14 Sensor Design Completed
2024-05-14 Project test results
    [BOM-sensor.csv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]

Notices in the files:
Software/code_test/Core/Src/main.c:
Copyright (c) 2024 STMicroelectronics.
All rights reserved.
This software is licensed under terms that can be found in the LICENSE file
